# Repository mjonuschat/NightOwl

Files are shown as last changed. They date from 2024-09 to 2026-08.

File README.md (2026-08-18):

# NightOwl: Integrated Dual Spool Filament Switching System

NightOwl is an enclosure that integrates multiple projects' technologies into a dual-spool filament switching system.

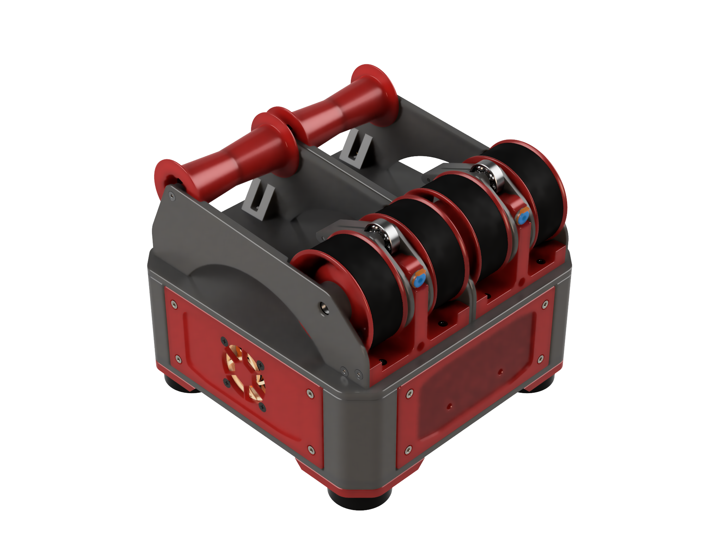
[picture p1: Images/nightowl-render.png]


## Summary

The goal of the NightOwl enclosure is to create a simple, universal filament switching solution that accommodates two primary usage styles: standalone units with integrated rewinding filament spool holders, or backpack-style units mountable to a printer, fed from separate spool rollers. A secondary objective was to design a mostly self-contained setup requiring only a 24V power supply and either a USB or CAN connection.

To achieve this, NightOwl integrates the following projects:

- Hartk's [Dual Nightwatch](https://github.com/hartk1213/MISC/tree/main/Voron%20Mods/Extruders/Dual_Nightwatch): a compact dual Bowden extruder based on the Voron Nightwatch
- [Sensored Y-Splitter/Hub](./Mods/D2F%20Hub/STL/NightOwl_Sensed_Hub_D2F.stl)
- [Filamentalist Rewinder - 80mm Axle](https://github.com/Enraged-Rabbit-Community/ERCF_v2/tree/master/Recommended_Options/Filamentalist_Rewinder) from the Enraged Rabbit Community
- Fysetc [ERB 2.0 MCU](https://github.com/FYSETC/FYSETC-ERB/tree/main/V2.0)
- ArmoredTurtle's [TurtleNeck](https://github.com/ArmoredTurtle/TurtleNeck) syncing toolhead buffer

Besides these parts you'll also want an extruder that has both a toolhead and an entry sensor. Some options for this are:

- [Clockwork 2](https://github.com/Enraged-Rabbit-Community/ERCF_v2/tree/master/Recommended_Options/Toolhead_Modifications/Stls)
- [WristWatch G2](https://github.com/bythorsthunder/Voron_Mods/tree/main/Wristwatch_G2_Dual_Filament_Sensor/STLs)

## Printing

Print the following components for the NightOwl.

- 1x Base plate
- 3x Blank Corner
- 1x Connector Corner
- 1x Connector Insert for your choice of connectors
- 1x Top Plate of choice (80mm Filamentalist or Backpack )
- 1x Y-Splitter Mount
- 4x Skirts
  - Front
  - Back
  - Left
  - Right
- 4x Feet (if using the Filamentalist top)
- 4x Knobs (if using the Backpack top)

## Other parts to print

- [Dual Nightwatch](https://github.com/hartk1213/MISC/tree/main/Voron%20Mods/Extruders/Dual_Nightwatch/STLs/Dual_Nightwatch)
  - Use the 2-part guidler, it has proven more reliable than the single piece guidler
  - Prefer the mid body with collets for improved reliability
- [Sensored Hub](./Mods/D2F%20Hub/STL/NightOwl_Sensed_Hub_D2F.stl)
- [Filamentalist](https://github.com/Enraged-Rabbit-Community/ERCF_v2/tree/master/Recommended_Options/Filamentalist_Rewinder)
  - Please use the files provided [in this repository](./STL/Filamentalist/), they are adjusted to fit slightly wider spools.
    Files in the directory are following the naming conventions in the manual and will yield the required two rewinders.

### Print Settings

All parts have been pre-oriented for support-free printing or include integrated supports. Print using the recommended Voron settings:

- Layer height: 0.2mm.
- Extrusion width: 0.4mm, forced.
- Infill percentage: 40%
- Infill type: grid, gyroid, honeycomb, triangle, or cubic.
- Wall count: 4
- Solid top/bottom layers: 5
- Supports: **NONE**

The skirts have been provided as 3MF files with the correct settings applied for PrusaSlicer. However, if your slicer does not support importing these settings, open the 3MF in geometry-only mode and change the type of the inlay/mesh modifier part to 'Modifier'. Then, configure the modifier settings as follows for optimal print results:

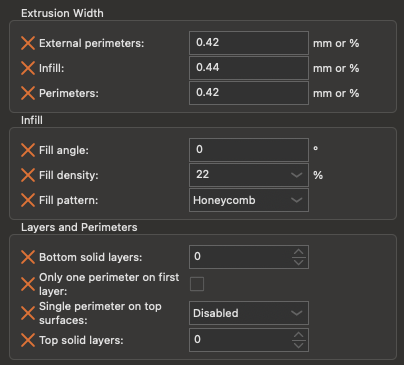
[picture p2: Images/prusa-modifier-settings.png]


## Assembly

### Bill of Materials

Please refer to the [Bill of Materials](./BOM.md) for a list of parts needed for the enclosure. Additionally, check the projects listed in the summary for specific parts requirements.

### Assembly Instructions

The [Assembly Manual](./Manual/NightOwl%20Assembly%20Manual.pdf) provides detailed, step-by-step instructions for assembling your NightOwl.

## Images

Soon(tm)

## Acknowledgements

The NightOwl project builds upon open-source innovations, drawing inspiration from the [BoxTurtle](https://github.com/ArmoredTurtle) project. While influenced by BoxTurtle's design philosophy, NightOwl distinguishes itself through deliberate design choices: minimal footprint, dual-channel limitation and leveraging off-the-shelf components.

## Changelog

- 2026-08-18 Documentation Updates
  - Added wiring diagrams for ERB 2.0
  - Updated pin-out to match AFC default config
  - Made the sensored hub the default choice
  - Removed the vendored macros/example config — AFC usage is now recommended
- 2025-02-03 NightOwl 1.0 (Flamboyant Flamingo)
  - Update front skirt (removed ECAS couplers)
- 2025-01-07 NightOwl RC.2 (Ethereal Elk)
  - Changed corners and top plates to use standard 6x3mm magnets
- 2024-11-29 NightOwl RC.1 (Derpy Dingo)
  - Included customized Filamentalist Parts
    - Parameters adjusted to allow for up to 74mm wide spools (instead of 68mm) with identical hardware.
  - Updated top panel to match the Filamentalist rewinders
  - Correctly tagged connector inserts with accent color
  - Fixed undersized hole in bottom panel
  - Fixed various quantities in the BOM
  - Made dual Micro-Fit connectors the recommended option
  - TurtleNeck is the default recommended filament tension sensor
- 2024-10-18 NightOwl Beta.1 (Crafty Crow)
  - Simplified the corners
    - Switch to an insert base approach for connectors
    - Single blank corner with universal mounting holes
    - Moved all connectors to the "back"
  - Added markers to the bottom plate where the various corners go
  - Added hints to parts printing for Nightwatch and Y-Splitter
  - Updated Bill of Materials with more sourcing links
- 2024-10-07 NightOwl Alpha.2 (Brawny Beaver)
  - Bill of Materials added
  - Increased height of enclosure by 4mm
  - Revised MCU mount to add support for BTT MMB 1.0 MCU
  - Added the option to use compressor feet
  - Updated to the latest dual nightwatch release (v16)
  - Moved MCU connectors to the back by default
    - Optional corners are provided to use XT30 2+2 or MicroFit 3.0 for the MCU connection
    - Optional corners to keep the MCU connection in the front corner (for backpack style use)
- 2024-09-25 NightOwl Alpha.1 (Ambitious Alpaca)

## License

This work is licensed under the GNU General Public License v3.0, for more details check the [LICENSE](./LICENSE).

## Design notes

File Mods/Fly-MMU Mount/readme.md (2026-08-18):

# Fly-MMU Mount
This allows mounting of the Fly-MMU.
Mount it so the board is furthest away from the holes for the cables. This is due to the odd position of the XT30 connector.

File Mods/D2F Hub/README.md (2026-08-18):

# D2F Hub for the Night Owl AFC

Sensored Hub for use with the AFC Klipper add-on, using a D2F switch and a 5.5mm ball bearing.

## Assembly

### Bill of Materials

- 1x D2F Switch
- 1x 5.5mm ball bearing ball
- 2x M2x10mm Self-Tapping Screw

## Acknowledgements

 - Created Robert Klotz [ArmoredTurtle](https://github.com/ArmoredTurtle), originally shared on the [VORON Discord](https://discord.com/channels/460117602945990666/1297434749157244968/1310841906376347739)

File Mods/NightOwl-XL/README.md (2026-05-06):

# NightOwl XL 

Modified parts for a single lane NightOwl that can support most 3-5kg spools.

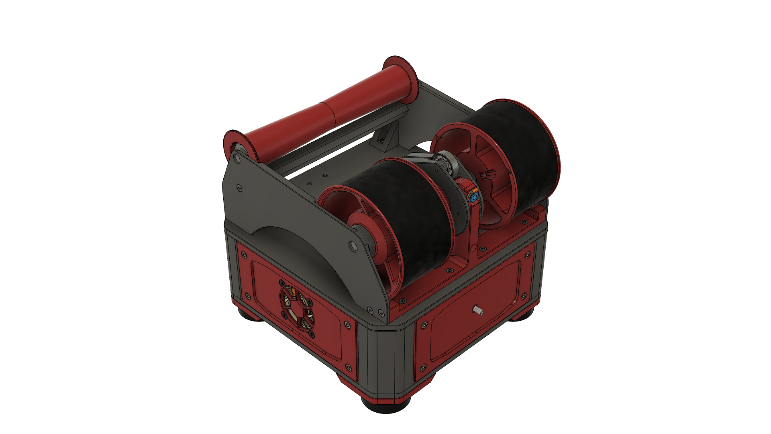
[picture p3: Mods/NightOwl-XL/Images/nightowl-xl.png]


## Summary

- XL Filamentalist that fits on the regular NightOwl top plate instead of the two 1kg versions
- Voron M4 Extruder, with entry & exit filament runout sensors
- Single lane front and rear skirts for M4 extruder

### Print Settings

All parts have been pre-oriented for support-free printing or include integrated supports. Print using the recommended Voron settings:

- Layer height: 0.2mm.
- Extrusion width: 0.4mm, forced.
- Infill percentage: 40%
- Infill type: grid, gyroid, honeycomb, triangle, or cubic.
- Wall count: 4
- Solid top/bottom layers: 5
- Supports: **NONE**

The skirts have been provided as 3MF files with the correct settings applied for PrusaSlicer. Follow the main printing instructions should you want/need to modify the settings.

## Assembly

### Bill of Materials

Please refer to the [Bill of Materials](./BOM.md) for a list of parts needed for the spool holder. This BOM includes all non-printed parts needed for the build including the Filamentalist XL and M4 Extruder.

## Images

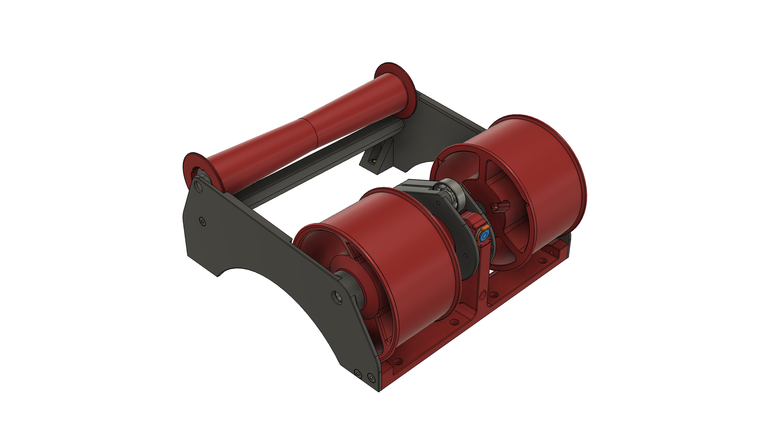
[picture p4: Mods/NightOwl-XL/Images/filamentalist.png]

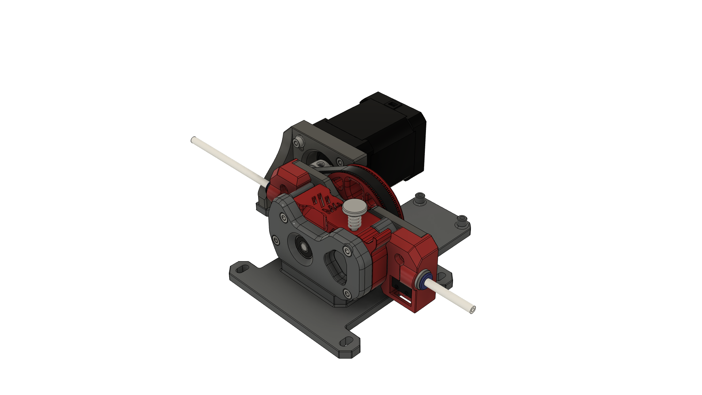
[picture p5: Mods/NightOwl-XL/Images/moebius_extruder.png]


## Acknowledgements

The modified M4 extruder is based on the excellent work of VORON Design and was done in cooperation with [hartk](https://github.com/hartk1213). 

## Changelog

- 2025-03-13 Initial Release

## License

This work is licensed under the GNU General Public License v3.0, for more details check the [LICENSE](../../LICENSE).

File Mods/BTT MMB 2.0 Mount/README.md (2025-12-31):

# Mount for BTT MMB 2.0 MCU

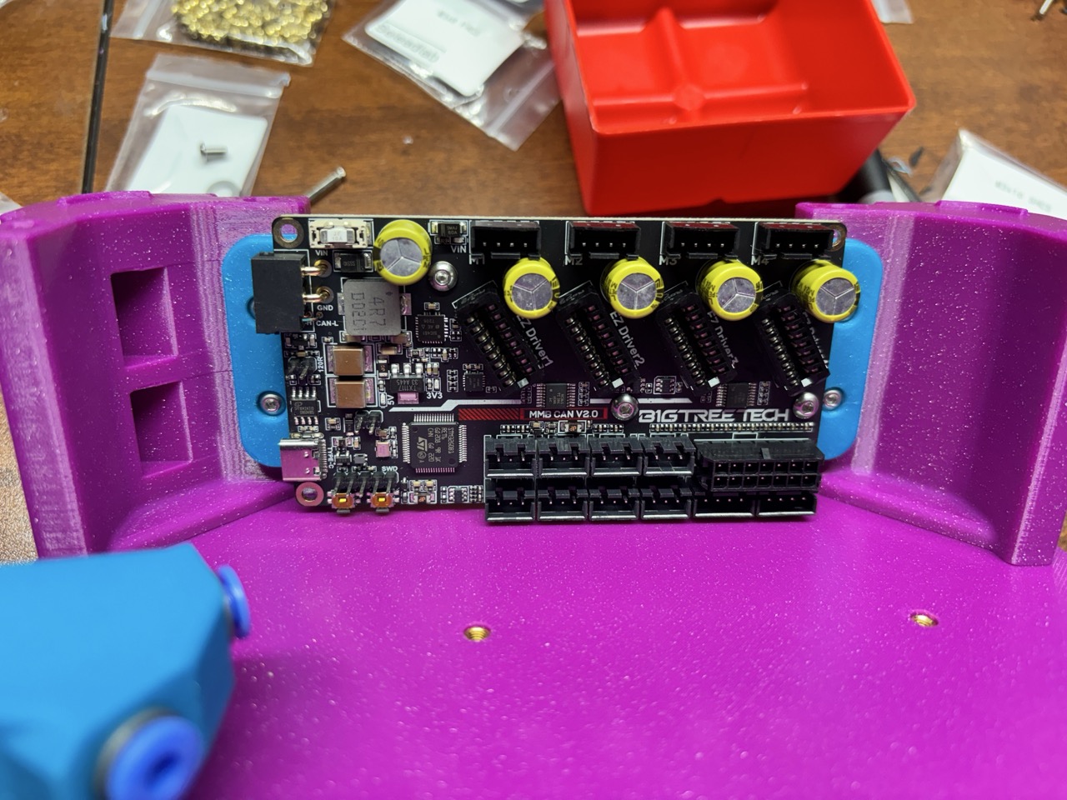
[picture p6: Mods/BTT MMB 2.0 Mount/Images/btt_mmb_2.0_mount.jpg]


### Print Settings

All parts have been pre-oriented for support-free printing or include integrated supports. Print using the recommended Voron settings:

- Layer height: 0.2mm.
- Extrusion width: 0.4mm, forced.
- Infill percentage: 20%
- Infill type: grid, gyroid, honeycomb, triangle, or cubic.
- Wall count: 4
- Solid top/bottom layers: 5
- Supports: **NONE*

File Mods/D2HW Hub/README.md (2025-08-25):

# D2HW Hub for the Night Owl AFC

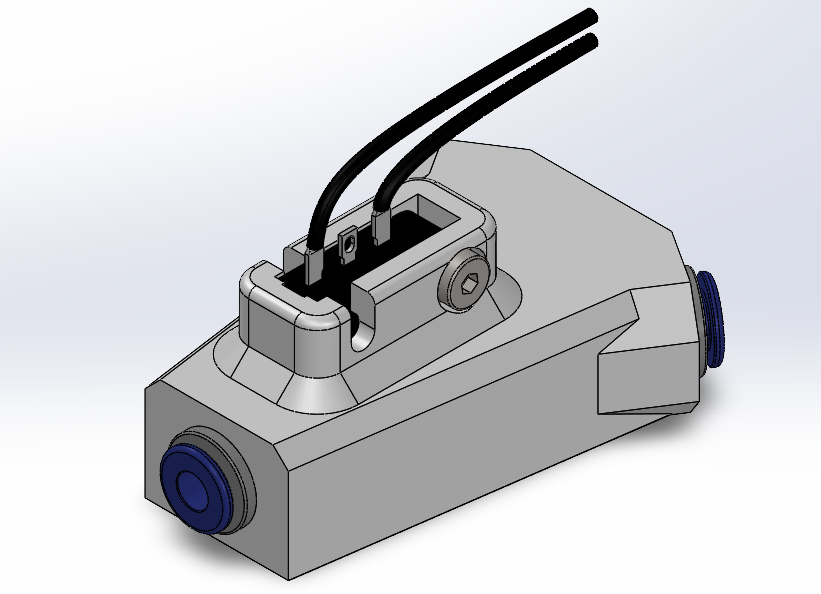
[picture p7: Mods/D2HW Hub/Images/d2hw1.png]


## A more reliable sensed Hub

Due to issues with the D2F hub and the 5.5mm Ball Bearing and them not always sensing the filament, I have created a hub based on the Box Turtle D2HW and MR63ZZ bearing method which is a lot more reliable. This will always trigger due to the short trigger and long stroke of the D2HW switch with the MR63ZZ bearing being 0.2mm from the bottom of the filament path.

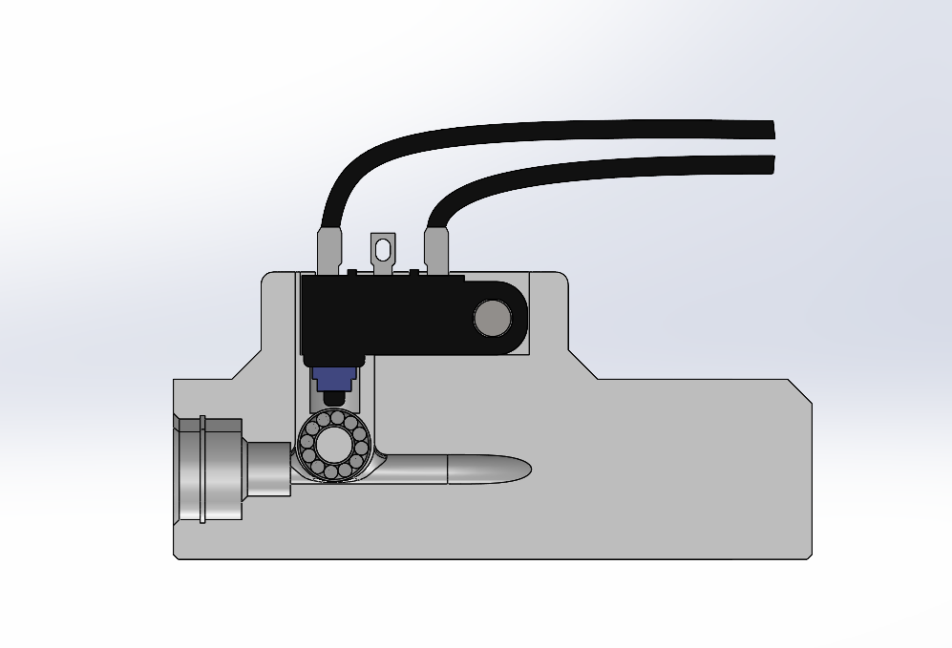
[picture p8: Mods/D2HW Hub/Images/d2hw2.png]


### Print Settings

All parts have been pre-oriented for support-free printing or include integrated supports. Print using the recommended Voron settings:

- Layer height: 0.2mm.
- Extrusion width: 0.4mm, forced.
- Infill percentage: 20%
- Infill type: grid, gyroid, honeycomb, triangle, or cubic.
- Wall count: 4
- Solid top/bottom layers: 5
- Supports: **NONE*

## Assembly

### Bill of Materials

- 1x [D2HW-C201H Switch](https://www.aliexpress.com/item/1005001866383478.html)
- 1x [MR63ZZ bearing](https://www.aliexpress.com/item/1005002121057437.html) - [MR63ZZ - Viper Worx](https://www.viperworx.uk/product/mr63zz-bearing)
- 3x [ECAS-04 Bowden Collet](https://www.aliexpress.com/item/1005006618335984.html) - [ECAS-04 - Viper Worx](https://www.viperworx.uk/product/ecas04-bowden-collet)
- 2x [M3x5x4 Heat Set Insert](https://www.aliexpress.com/item/1005003582355741.html) - [M3x5x4 Heat Set Insert - Viper Worx](https://www.viperworx.uk/product/heat-set-inserts-m3x5x4)
- 1x M3x10 Socket Head Cap Screw

## Acknowledgements

 - Robert Klotz [ArmoredTurtle](https://github.com/ArmoredTurtle) for the idea of using a D2HW switcha and MR63ZZ Bearing for sensing filament.

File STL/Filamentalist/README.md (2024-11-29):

# The "Filamentalist" Passive Filament Driven Rewinder

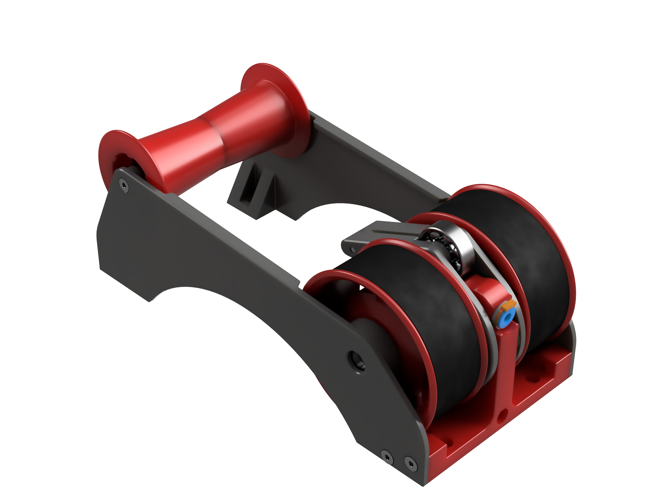
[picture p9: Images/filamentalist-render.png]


This folder contains STL files tailored for the NightOwl use of the Filamentalist, featuring adjusted parameters to accommodate spools up to 74mm wide (versus the standard 68mm), without requiring hardware modifications.

## Attention

- Only the necessary files for the NightOwl project are provided here.
- File naming conventions adhere to Voron standards.
- Quantities in file names are set to print a pair of Filamentalist rewinders.

## Parameters for Export

The export parameters are listed in the [ExportedParameters](./Parameters/ExportedParameters.csv) file. You can import these parameters into Fusion 360 for further adjustments.

## Original Source

Find the Filamentalist CAD and unmodified files in the [ERCFv2](https://github.com/Enraged-Rabbit-Community/ERCF_v2/tree/master/Recommended_Options/Filamentalist_Rewinder) GitHub repository: (link unavailable). These files in this directory were exported from CAD version 3.0.5.

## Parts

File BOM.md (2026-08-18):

# BOM

## NightOwl Enclosure

Item | Qty | Notes
--- | --- | ---
M3 Heatsets | 48 | [AliExpress](https://www.aliexpress.us/item/3256806130510484.html)
M3x6 BHCS | 8 | [AliExpress](https://www.aliexpress.us/item/2251832624537980.html)
M3x8 FHCS | 8 | [AliExpress](https://www.aliexpress.us/item/2251832747871730.html)
M3x6 SHCS | 18 | [AliExpress](https://www.aliexpress.us/item/2251832624557792.html)
M3x8 SHCS | 10 | [AliExpress](https://www.aliexpress.us/item/2251832624557792.html)
M3x12 SHCS | 8 | [AliExpress](https://www.aliexpress.us/item/2251832624557792.html)
M3x16 SHCS | 2 | [AliExpress](https://www.aliexpress.us/item/2251832624557792.html)
M5x20 BHCS | 4 | [AliExpress](https://www.aliexpress.us/item/2251832624537980.html)
M5 Hexnut | 4 | [AliExpress](https://www.aliexpress.us/item/2251832681933100.html)
M5 Washer | 4 | [AliExpress](https://www.aliexpress.us/item/3256802114850018.html)
Rubber Compressor Foot | 4 | [AliExpress](https://www.aliexpress.us/item/3256801282730627.html)
6x3mmm N52 Disc Magnet | 16 | [AliExpress](https://www.aliexpress.us/item/3256806616466149.html)
Molex Microfit 436400400 | 2 | [DigiKey](https://www.digikey.com/en/products/detail/molex/0436400400/268981)
Molex Microfit 436450400 | 2 | [DigiKey](https://www.digikey.com/en/products/detail/molex/0436450400/268976)
Molex Microfit Female Pin 430300007 | 8 | [DigiKey](https://www.digikey.com/en/products/detail/molex/0430300007/252479)
Molex Microfit Male Pin 430310007 | 8 | [DigiKey](https://www.digikey.com/en/products/detail/molex/0430310007/252483)
4010 Axial Fan | 1 | [AliExpress](https://www.aliexpress.us/item/2251832541552769.html)
ST-Fan Screw | 4 | [AliExpress](https://www.aliexpress.us/item/3256801122413512.html)
Fysetc ERB 2.0 | 1 | [AliExpress](https://www.aliexpress.us/item/3256807024596241.html)
PTFE Tube (2.5mm/4mm) | 1m | [AliExpress](https://www.aliexpress.us/item/3256807251789429.html)

### Notes

- Connectors: You can replace one pair of Micro-Fit 3.0 connectors with a set of AMass XT30 2+2 connectors to make using prefabricated CAN cables easier.

## Filamentalist Rewinder (80mm)

For convenience you can order the following kit instead of sourcing the individual parts from the Filamentalist BOM:

Item | Qty | Notes
--- | --- | ---
80mm Filamentalist Kit | 2 | [AliExpress](https://www.aliexpress.us/item/3256807145086311.html)

## Miscellaneous Bits & Pieces

These are sourcing links for known good components used by some of the incorporated projects. For quantities check the respective BOM documents.

Item | Notes
---  | ---
KW10 Microswitch (D2F compatible) | [AliExpress](https://www.aliexpress.us/item/3256806868797694.html)
5.5mm Ball Bearing Balls | [Amazon](https://www.amazon.com/gp/product/B078T81JK3)

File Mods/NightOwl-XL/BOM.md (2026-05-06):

# BOM

## NightOwl XL

Item | Qty | Notes
--- | --- | ---
M3 Heatsets (M3x5Dx4L) | 56 | [AliExpress](https://www.aliexpress.us/item/3256806130510484.html)
M3x6 SHCS | 18 | [AliExpress](https://www.aliexpress.us/item/2251832624557792.html)
M3x8 SHCS | 11 | [AliExpress](https://www.aliexpress.us/item/2251832624557792.html)
M3x12 SHCS | 11 | [AliExpress](https://www.aliexpress.us/item/2251832624557792.html)
M3x16 SHCS | 2 | [AliExpress](https://www.aliexpress.us/item/2251832624557792.html)
M3x30 SHCS | 4 | [AliExpress](https://www.aliexpress.us/item/2251832624557792.html)
M3x35 SHCS | 1 | [AliExpress](https://www.aliexpress.us/item/2251832624557792.html)
M3x6 BHCS | 11 | [AliExpress](https://www.aliexpress.us/item/2251832624537980.html)
M3x8 BHCS | 13 | [AliExpress](https://www.aliexpress.us/item/2251832624537980.html)
M5x20 BHCS | 4 | [AliExpress](https://www.aliexpress.us/item/2251832624537980.html)
M3x8 FHCS | 14 | [AliExpress](https://www.aliexpress.us/item/2251832747871730.html)
M3x18 FHCS | 3 | [AliExpress](https://www.aliexpress.us/item/2251832747871730.html)
M5 Hexnut | 4 | [AliExpress](https://www.aliexpress.us/item/2251832681933100.html)
M3 Washer | 3 | [AliExpress](https://www.aliexpress.us/item/2251832626221739.html)
M5 Washer | 4 | [AliExpress](https://www.aliexpress.us/item/2251832626221739.html)
M5 x 1mm x 10mm Shim | 1 | [AliExpress](https://www.aliexpress.us/item/3256802114850018.html)
ST-Fan Screw | 4 | [AliExpress](https://www.aliexpress.us/item/3256804302276719.html)
6x3mmm N52 Disc Magnet | 16 | [AliExpress](https://www.aliexpress.us/item/3256811348559597.html)
8mm x 180mm Steel Rod | 2 | [Amazon](https://www.amazon.com/dp/B08FBSYYW4)
HF081412 ONE Way Needle Roller Bearing | 1 |  [Amazon](https://www.amazon.com/dp/B09BMP9X37)
HK0810 needle roller bearing (for regular idler roller) | 2 | [Amazon](https://www.amazon.com/dp/B07GC8VTPV)
688-2RS bearing (for alternative idler roller) | 2 | [Amazon](https://www.amazon.com/dp/B082PQ3SC4)
608zz bearing | 4 | [Amazon](https://www.amazon.com/dp/B07C6FL8TW)
Rubber Compressor Foot | 4 | [AliExpress](https://www.aliexpress.us/item/3256803000161440.html)
D2F-L Switch | 2 | [Amazon](https://www.amazon.com/dp/B088W8WMTB)
ECAS pneumatic fittings | 4 | [AliExpress](https://www.aliexpress.us/item/3256802352042527.html)
ECAS pneumatic clips | 4 | [AliExpress](https://www.aliexpress.us/item/2255800159625996.html)
Coil spring - 0.5x4x25mm (pen) | 1 | [Amazon](https://www.amazon.com/dp/B076LNJF5Q)
5.5mm steel ball-bearing | 2 | [Amazon](https://www.amazon.com/dp/B09DSH1GL6)
NEMA17 Motor 17HS15-1504S1 | 1 | [StepperOnline](https://www.omc-stepperonline.com/nema-17-bipolar-45ncm-63-74oz-in-1-5a-42x42x39mm-4-wires-w-1m-cable-connector-17hs15-1504s1)
BMG Gear set | 1 | [AliExpress](https://www.aliexpress.us/item/2255799834871688.html)
BMG Thumbscrews | 1 | [AliExpress](https://www.aliexpress.us/item/2251832761377061.html)
EBB 36/42 | 1 | [Biqu](https://biqu.equipment/products/bigtreetech-ebb-36-42-can-bus-for-bigtreetech-ebb-36-42-can-bus-u2c-v2-1-for-connecting-klipper-expansion-device-support-pt1000connec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)
GT2 Belt Loop (6mm wide) - 188mm | 1 | [AilExpress (Powage)](https://www.aliexpress.us/item/2255799847707082.html)
GT2 20T Pulley (5mm bore, 6mm wide) | 2 | [AilExpress (Powage)](https://www.aliexpress.us/item/2251832040247568.html)
Molex Microfit 436400400 4 female | 2 | [DigiKey](https://www.digikey.com/en/products/detail/molex/0436400400/268981)
Molex Microfit 436450400 4 male | 2 | [DigiKey](https://www.digikey.com/en/products/detail/molex/0436450400/268976)
Molex Microfit Female Pin 430300007 | 8 | [DigiKey](https://www.digikey.com/en/products/detail/molex/0430300007/252479)
Molex Microfit Male Pin 430310007 | 8 | [DigiKey](https://www.digikey.com/en/products/detail/molex/0430310007/252483)
4010 Axial Fan 5V | 1 | [AliExpress](https://www.aliexpress.us/item/2251832541552769.html)
Filamentalist Rubbber Band | 2 | [Amazon](https://www.amazon.com/dp/B09B14T1KS)
O-Ring #211 (20mmID x 26mmOD) | 2 | [AliExpress](https://www.aliexpress.us/item/3256804251890269.html)
PTFE Tube (2.5mm/4mm) | 1m | [AliExpress](https://www.aliexpress.us/item/3256807251789429.html)

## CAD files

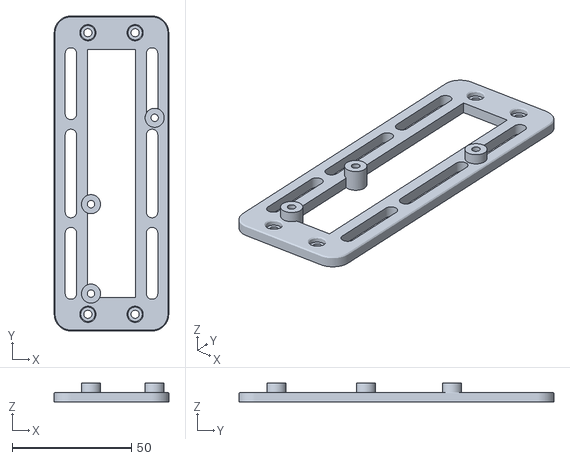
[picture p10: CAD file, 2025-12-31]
Mods/BTT MMB 2.0 Mount/STL/BTT MMB 2.0 Mount.stl
48.0 x 132.0 x 7.80

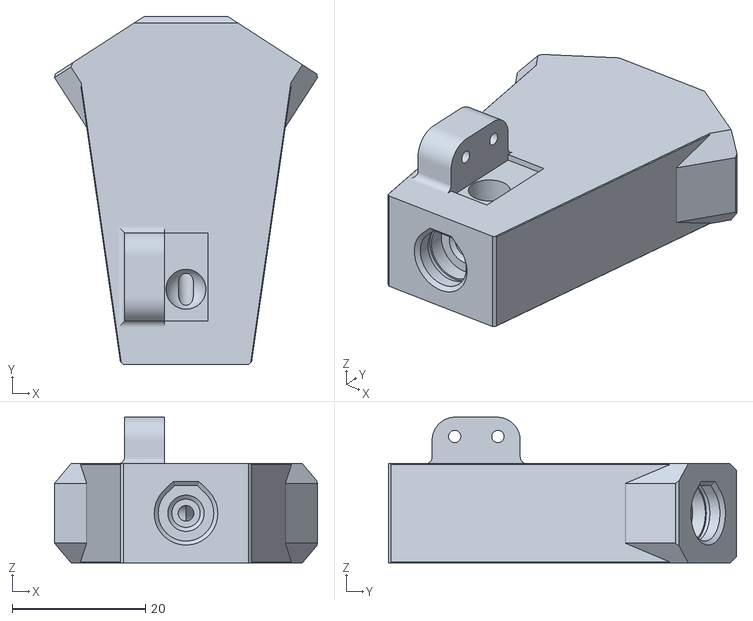
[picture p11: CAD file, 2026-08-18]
Mods/D2F Hub/STL/NightOwl_Sensed_Hub_D2F.stl
39.5 x 52.3 x 21.9

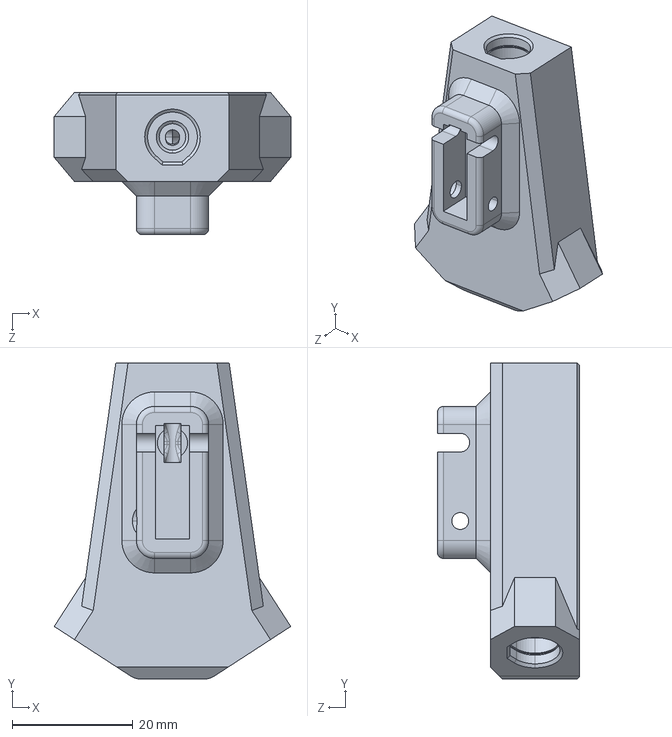
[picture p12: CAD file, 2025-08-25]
Mods/D2HW Hub/CAD/Night Owl D2HW Hub.STEP
39.2 x 52.4 x 23.6 mm

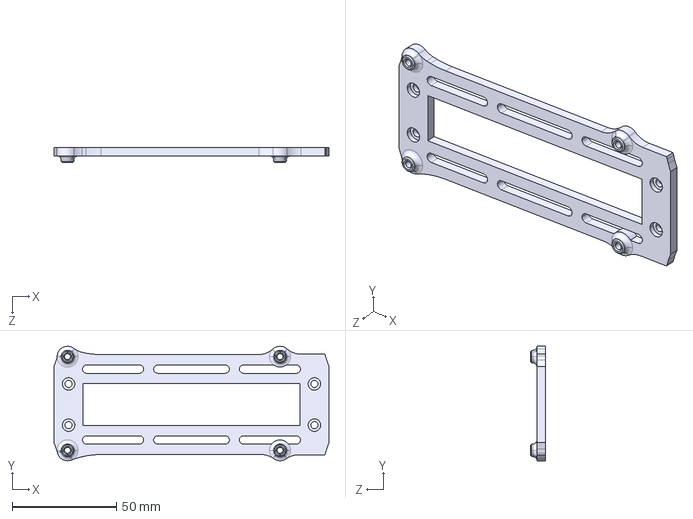
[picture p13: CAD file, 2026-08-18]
Mods/Fly-MMU Mount/CAD/Fly-MMU Mount.STEP
132.0 x 55.0 x 7.00 mm

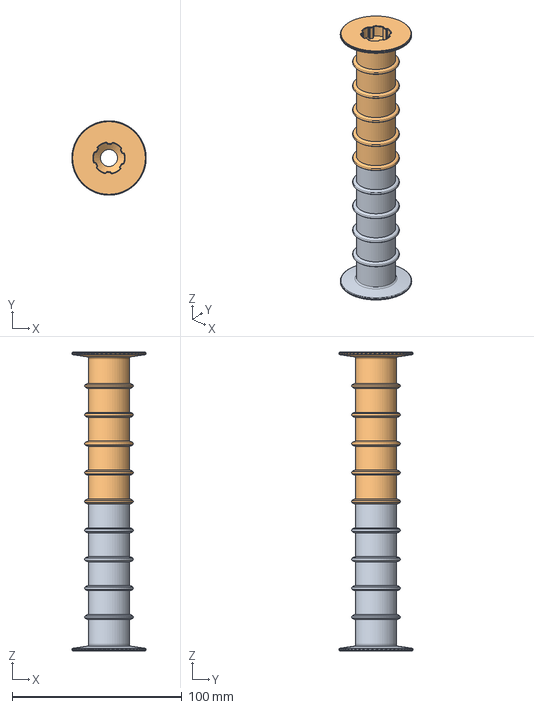
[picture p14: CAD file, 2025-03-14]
Mods/NightOwl-XL/CAD/Alternative Idler Roller.step
43.8 x 43.8 x 176.0 mm
Idler Roller - Male
Idler Roller - Female

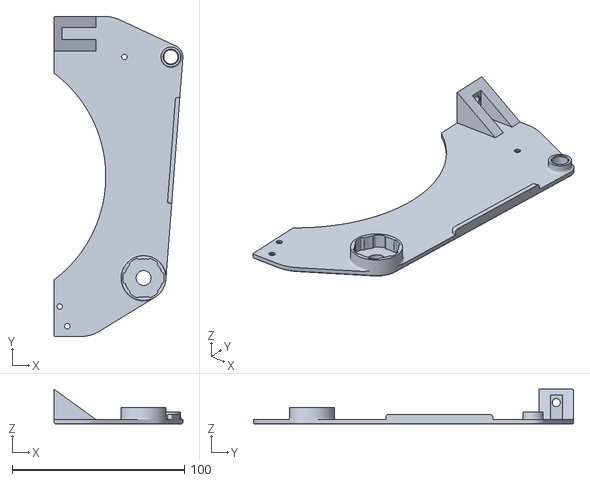
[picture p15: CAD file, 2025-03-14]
Mods/NightOwl-XL/STL/Filamentalist XL/left_support.stl
74.8 x 186.0 x 20.1

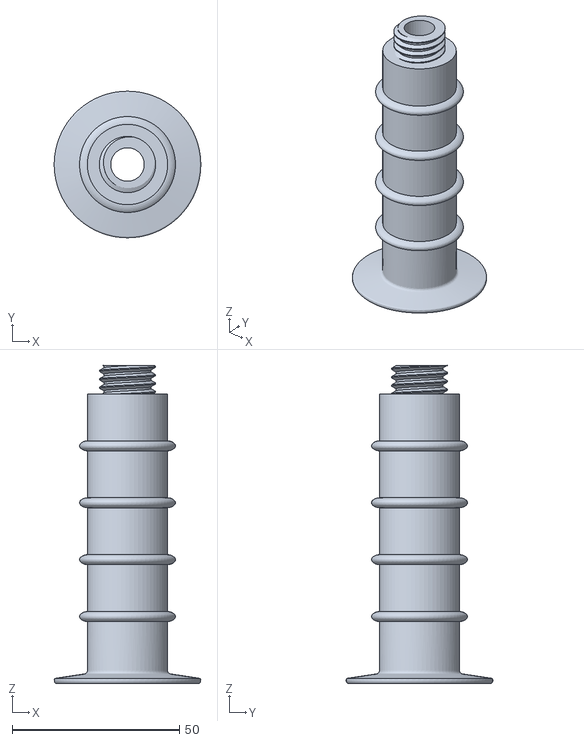
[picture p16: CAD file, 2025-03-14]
Mods/NightOwl-XL/STL/Filamentalist XL/Options/[a]_idler_roller_male_sections.stl
43.8 x 43.8 x 95.0

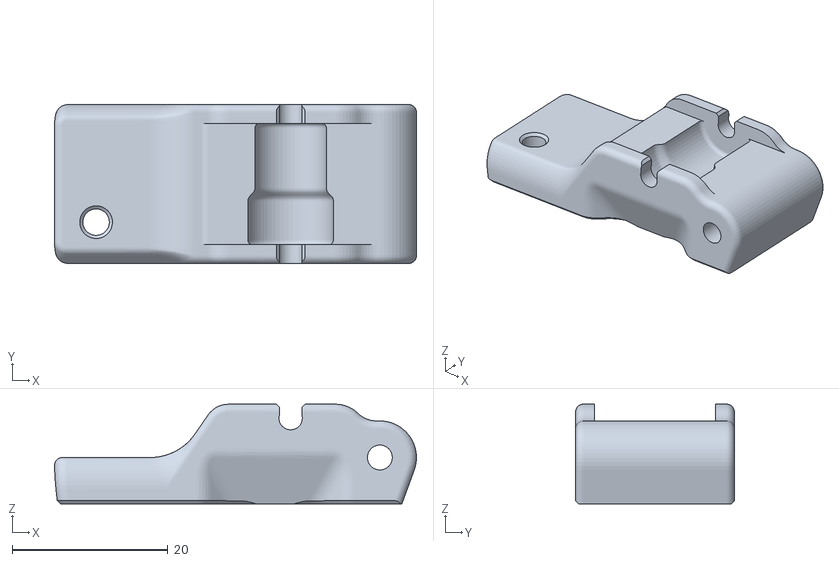
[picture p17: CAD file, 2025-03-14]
Mods/NightOwl-XL/STL/M4 Extruder/[a]_guidler_arm.stl
46.5 x 20.4 x 12.8

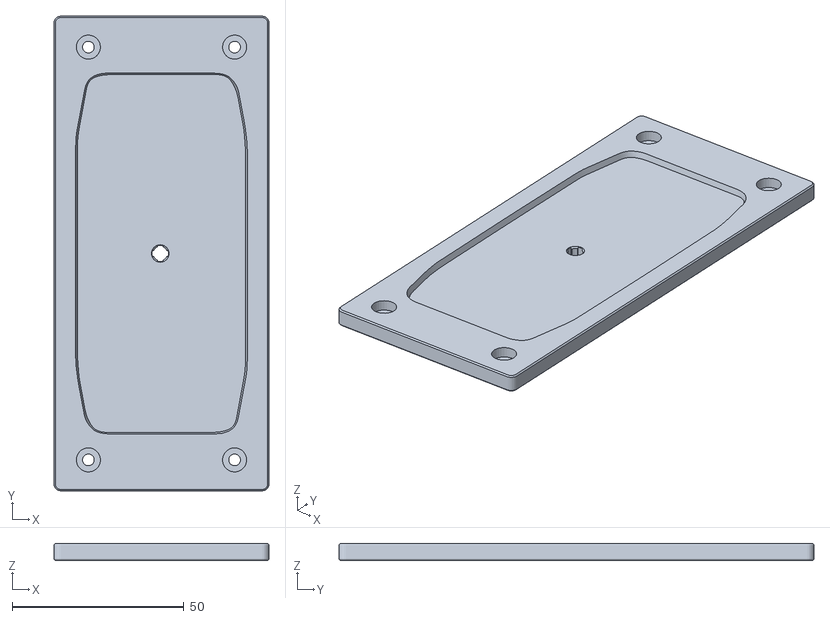
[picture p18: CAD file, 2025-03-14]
Mods/NightOwl-XL/STL/Skirts/[a]_front_skirt_m4.stl
62.5 x 138.0 x 5.00

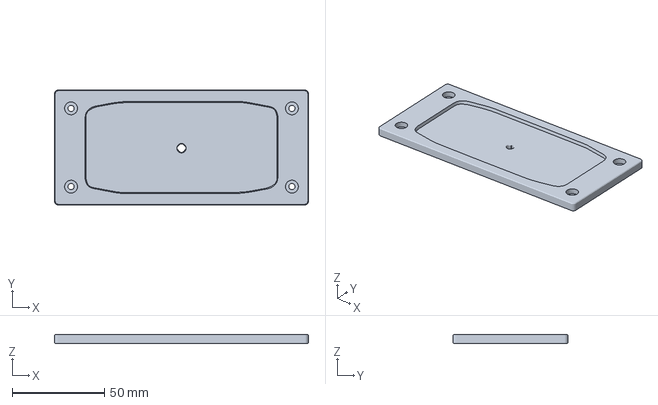
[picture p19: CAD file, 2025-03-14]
Mods/NightOwl-XL/STL/Skirts/Pre-Sliced/[a]_rear_skirt_m4.3mf
138.0 x 62.5 x 5.00 mm

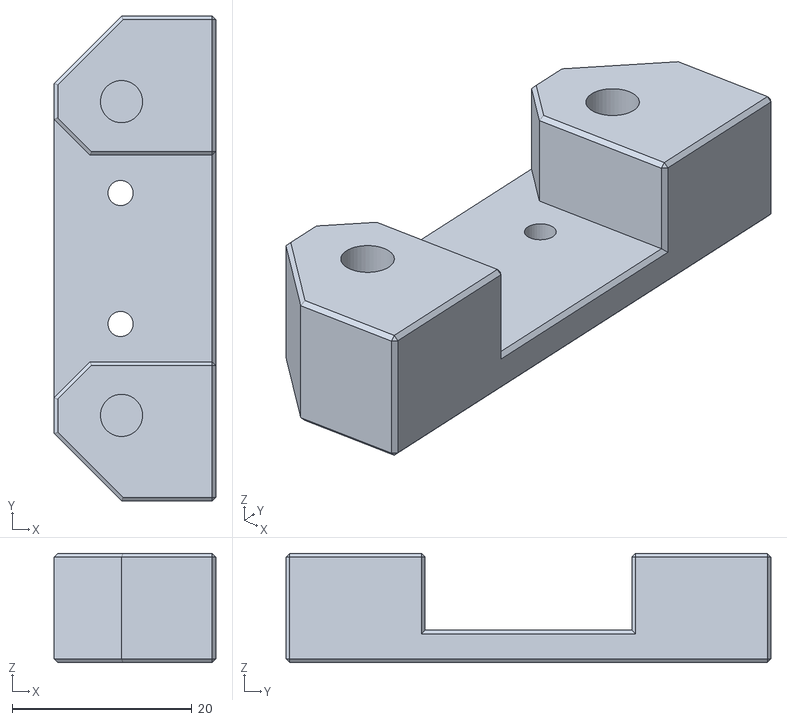
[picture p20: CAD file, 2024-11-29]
STL/Accessories/y_splitter_mount.stl
18.0 x 54.0 x 12.1

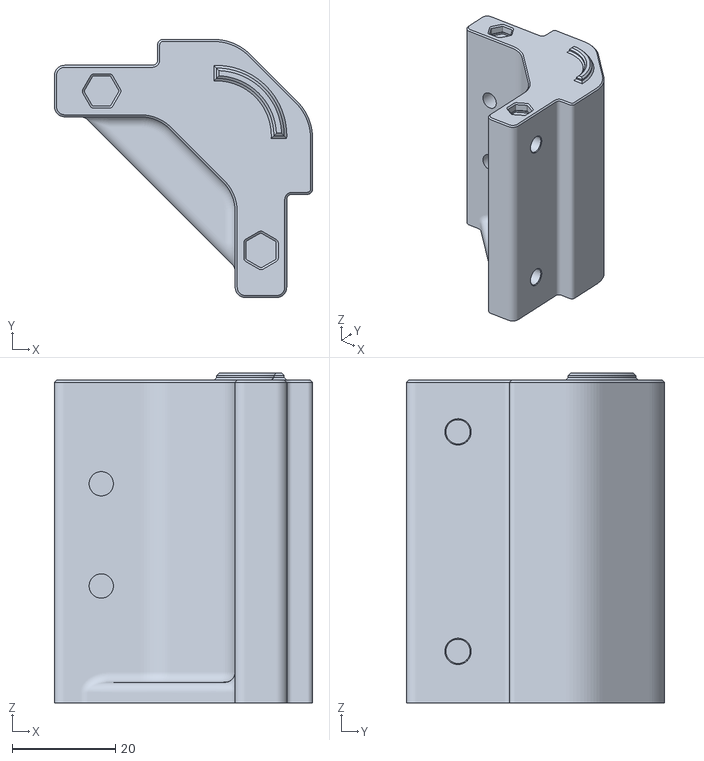
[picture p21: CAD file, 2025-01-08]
STL/Corners/corner_blank_x3.stl
50.0 x 50.0 x 63.9

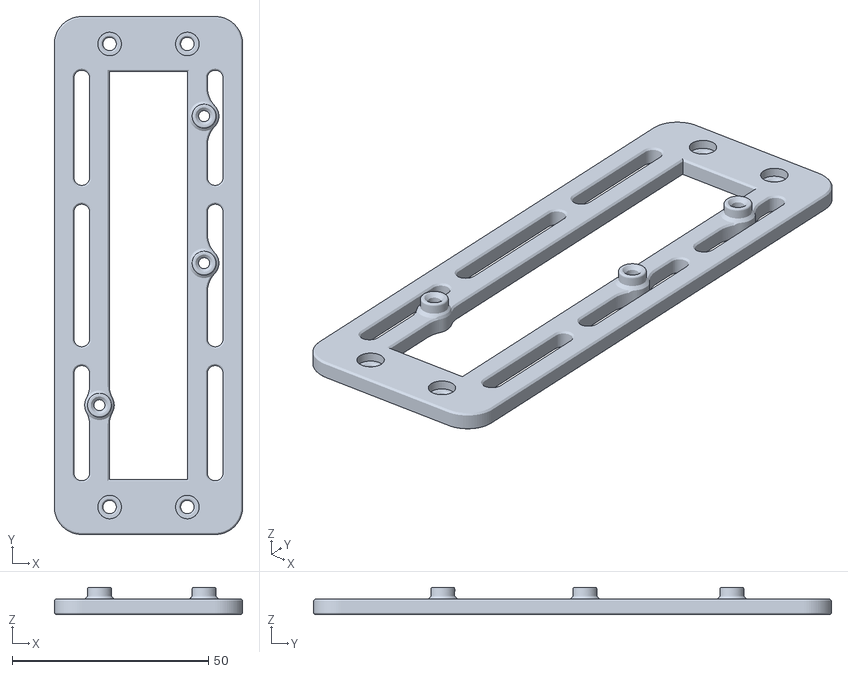
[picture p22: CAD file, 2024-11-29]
STL/Electronics/mcu_mount_fysetc_erb2.stl
48.0 x 132.0 x 7.00

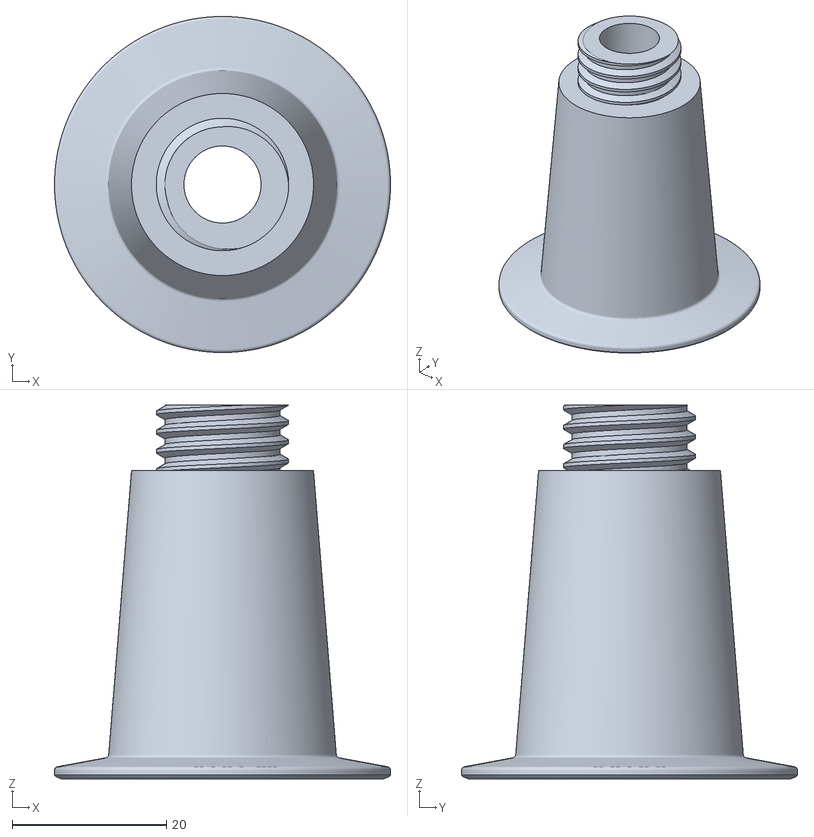
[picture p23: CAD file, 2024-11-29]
STL/Filamentalist/[a]_idler_roller_male_x2.stl
43.6 x 43.6 x 48.5

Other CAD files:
STL/Panels/top_panel_filamentalist.stl
STL/Skirts/[a]_skirt_front.stl
STL/Skirts/Pre-Sliced/[a]_front.3mf
Mods/NightOwl-XL/CAD/Skirts.step
Mods/D2HW Hub/STL/Night Owl D2HW Hub.stl
Mods/Fly-MMU Mount/CAD/Fly-MMU Mount.SLDPRT
Mods/Fly-MMU Mount/STL/Fly-MMU Mount.STL
Mods/NightOwl-XL/STL/Filamentalist XL/Options/[a]_idler_roller_female_sections.stl
Mods/NightOwl-XL/STL/Filamentalist XL/[a]_center_drive_roller.stl
Mods/NightOwl-XL/STL/Filamentalist XL/[a]_idler_roller_female.stl
Mods/NightOwl-XL/STL/Filamentalist XL/[a]_idler_roller_male.stl
Mods/NightOwl-XL/STL/Filamentalist XL/[a]_rim_roller_x2.stl
Mods/NightOwl-XL/STL/Filamentalist XL/[a]_tensioner_mount.stl
Mods/NightOwl-XL/STL/Filamentalist XL/axle_depth_tool.stl
Mods/NightOwl-XL/STL/Filamentalist XL/cdr_spacer_x2.stl
Mods/NightOwl-XL/STL/Filamentalist XL/rear_brace.stl
Mods/NightOwl-XL/STL/Filamentalist XL/right_support.stl
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

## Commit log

2024-09-26 Initial release (alpha.1)
    [Base - Dual Nightwatch.stl, Top Panel (80mm Filamentalist).stl, Top Panel (Backpack + Knobs).stl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]
2024-10-08 NightTurtle alpha.2 release (Brawny Beaver)
    [Base - Dual Nightwatch.stl, Top Panel (80mm Filamentalist).stl, Top Panel (Backpack + Knobs).stl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]
2024-10-19 docs: Fix typo in BOM
2024-10-19 docs: Add more sourcing links to BOM
2024-10-20 fix: Release NightOwl Beta.1
    [[a]_foot_x4.stl, [a]_front.3mf, [a]_left.3mf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]
2024-10-23 docs: More sourcing links for magnets
2024-10-23 docs: Add TurtleNeck syncing toolhead buffer
2024-10-24 fix: Remove extra feet from STL
    [[a]_foot_x4.stl]
2024-10-25 docs: Highlight magnet polarity requirements
2024-10-28 fix: Undersized mounting hole in bottom plate
    [bottom_panel.stl]
2024-10-28 fix: Naming of microfit connector inserts
    [connector_insert_dual_microfit.stl, connector_insert_single_microfit.stl]
2024-11-19 docs: Update belay wiring instructions
2024-11-29 docs: Update rendering with latest filamentalist
2024-11-29 docs: Fix quantities in BOM
2024-11-29 Updated STL files for rc.1 release
    [[a]_connector_insert_dual_microfit.stl, [a]_connector_insert_single_microfit.stl, [a]_connector_insert_xt30_microfit.stl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]
2024-11-29 Add STL files for adjusted Filamentalist rewinders
    [ExportedParameters.csv, [a]_center_drive_roller_x2.stl, [a]_idler_roller_axle_x2.stl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]
2024-11-29 docs: Add assembly manual
2024-11-29 docs: Make TurtleNeck the preferred filament tension sensor
2024-11-29 Update CAD for RC.1
2024-12-05 docs: Fixes for assembly manual
2024-12-05 docs: Add M5 washers to BOM
2024-12-05 docs: Add PTFE Tube to BOM
2024-12-23 docs: mention adjusted Filamentalist
2024-12-23 docs: Update the printing instructions for the Filamentalist
2024-12-24 Update BOM.md
    Added Microfit3 pins
2025-01-08 Update STL files for RC.2 release
    [corner_blank_x3.stl, corner_connectors.stl, top_panel_backpack.stl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]
2025-01-08 Update CAD for rc.2 release
2025-01-08 docs: Update BOM for rc.2 release
2025-01-08 Fix STL orientation for printing
    [corner_blank_x3.stl, corner_connectors.stl, top_panel_backpack.stl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]
2025-02-04 New front skirt (no ECAS couplers)
    [[a]_front.3mf, [a]_skirt_front.stl, [a]_skirt_front_modifier.stl]
2025-02-04 Update CAD for 1.0 release
2025-02-04 Update BOM for 1.0 release
2025-02-04 Update assembly manual for 1.0 release
2025-02-05 docs: Update rendering in assembly manual
2025-03-14 Mod: NightOwl XL for 3-5kg spools
    [Alternative Idler Roller.step, Skirts.step, [a]_5x4mm_spacer.stl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]
2025-08-25 Add D2HW Hub
    [Night Owl D2HW Hub.STEP, Night Owl D2HW Hub.stl]
2025-12-11 Upload BTT MMB 2.0 MCU Mount
2025-12-31 Organize BTT MMB 2.0 mount usermod
    [BTT MMB 2.0 Mount.stl]
2026-05-06 docs: Add NightOwl-XL BOM
